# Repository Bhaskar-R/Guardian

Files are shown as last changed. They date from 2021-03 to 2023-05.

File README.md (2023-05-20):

<p align="center">
  <a href="https://github.com/Bhaskar-R/Automated-Hydroponics-System">
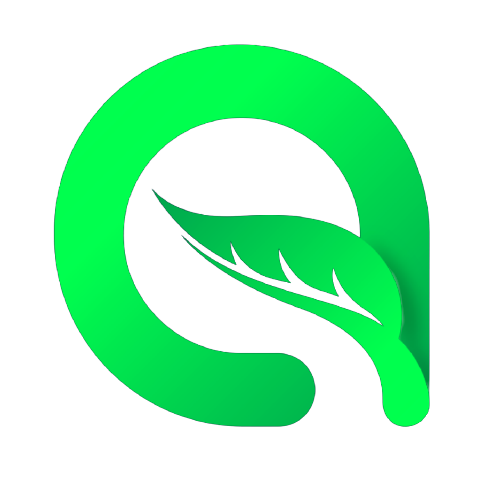
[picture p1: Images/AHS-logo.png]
AHS logo
    
  </a>
</p>

<h2 align="center">Guardian</h2>

<p align="center">Guardian is an advanced, fully automated hydroponics system designed to optimize plant growth and maximize yield. Utilizing micro-controllers and pH fuzzy logic control, it ensures precise nutrient delivery, enables remote monitoring, and achieves remarkable water savings while increasing crop productivity. 
</p>
<br>



## Table of contents
- [Render](#Render-of-Guardian)
- [Parameters Measured](#Parameters-Measured)
- [DataBase](#DataBase)
- [Controllable Parameters](#Controllable-Parameters)
    - [Motors and Light](#Motors-and-Light)
    - [Humidity and Temperature](#Humidity-and-Temperature)
    - [Light Interval](#Light-Interval)
    - [Motor Running Duration](#Motor-Running-Duration)
- [The Schematic diagram](#The-Schematic-diagram)
    - [Master Board](#The-Schematic-Diagram-of-Master-board)
    - [Slave Board](#The-Schematic-of-Slave-Board)
- [PCB Layout](#PCB-Layout)
    - [Master Board](#The-PCB-Layout-of-Master-board)
    - [Slave Board](#The-PCB-Layout-of-Slave-board)
- [Building the Hardware](#Building-the-Hardware)
    - [Master Board](#Master-Board)
    - [Total Setup](#Total-Setup-Overview)
- [I2CSB Library](#Using-`I2CSB`-library)
    - [Adding Library](#How-to-add-the-library)
    - [Functions](#How-to-use-the-functions-in-the-library)
    - [Handling the Errors and Miscommunication](#Handling-the-Errors-and-Miscommunication)
    - [Communication definitions](#The-communication-definition)
- [EEPROM Database](#Using-EEPROM-Database)
    - [Functions](#Functions)
    - [Usage](#Usage)
- [Control System](#Control-System)
- [Sample of Guardian](#Sample-of-Guardian)
- [License](#License)

## Render of Guardian
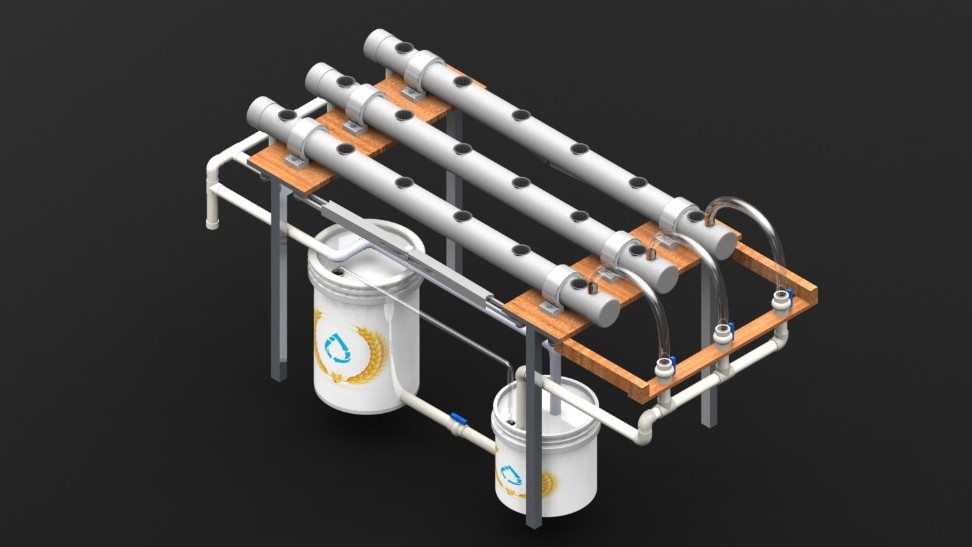
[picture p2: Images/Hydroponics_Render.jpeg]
Render


## Parameters Measured
* Temperature (DHT)
* Humidity (DHT)
* Tank Water Level
* Reservoir Water Level
* Plant Motor
* Reservoir Motor
* Mist Motor
* Lighting  

## DataBase
- Any DataBase can used to store the Data and control the System Remotely
- For this project I have used FireBase - A Realtime DataBase

A Few Pictures of FireBase
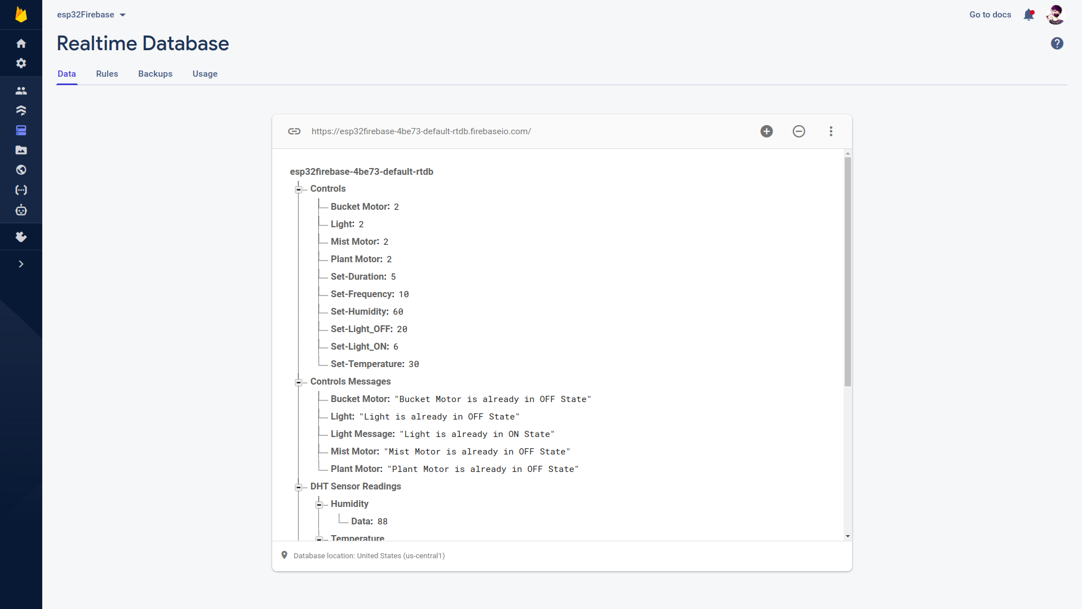
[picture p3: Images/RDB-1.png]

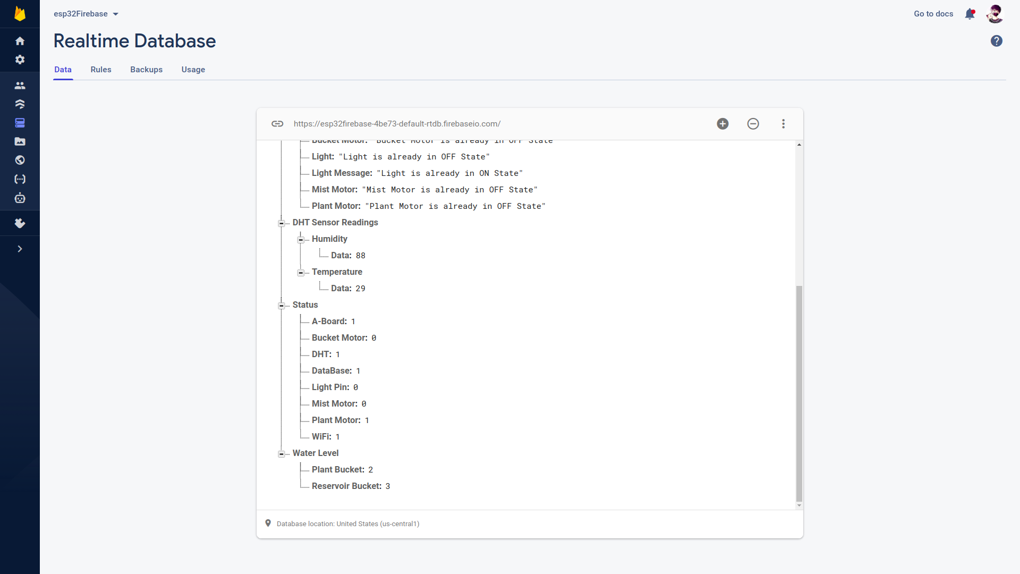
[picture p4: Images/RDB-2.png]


## Controllable Parameters  

### Motors and Light

There are two Modes for Controlling the Motors and lighting

|Digits |Status |Mode|
|---|---|----|
|0 |Off |Manual Override Mode ON | 
|1 |On |Manual Override Mode ON | 
|2 | - |Manual Override Mode OFF| 

### Humidity and Temperature

We can Manually Control/ Automate the Threshold Values of Humidity and Temperature as per the crop  

### Light Interval 
We can Manually control/ Automate the Intervals of Lighting to control the Temperature as per the requirements of the crop 

### Motor Running Duration
We can Manually control/ Automate the Intervals of running Plant Motor for regular watering as per the requirements of the crop 

## The Schematic diagram
The Schematic and PCB designs are made using KiCAD. Find the files here: [KiCad_PCB_design](PCB_designs/KiCad_PCB_design/)
### The Schematic Diagram of Master board
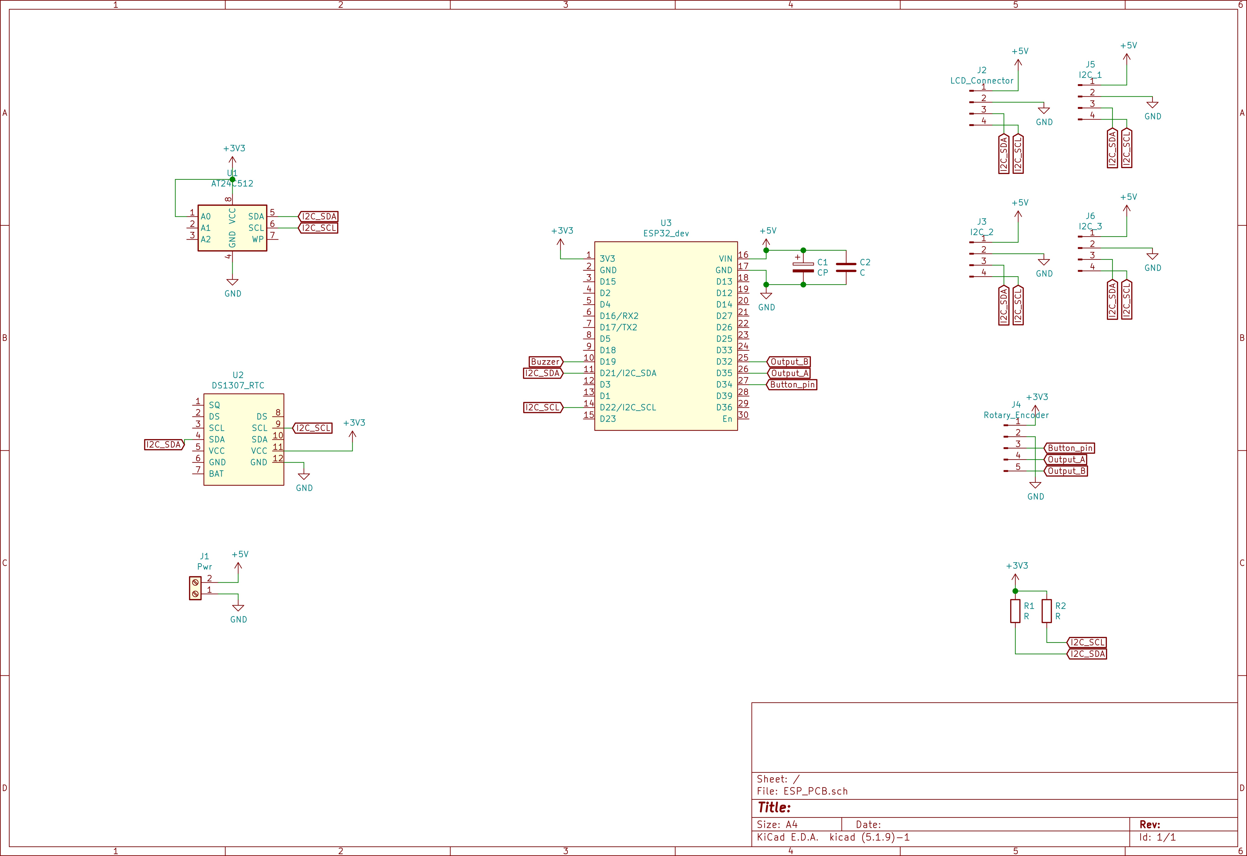
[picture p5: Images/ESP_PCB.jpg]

* The Master board has an ESP32, DS1307 RTC clock, AT24C512 EEPROM and an I2C LCD display.
* The Master board has a JST connecter port to connect to slave board. 

<br>

### The Schematic of Slave Board
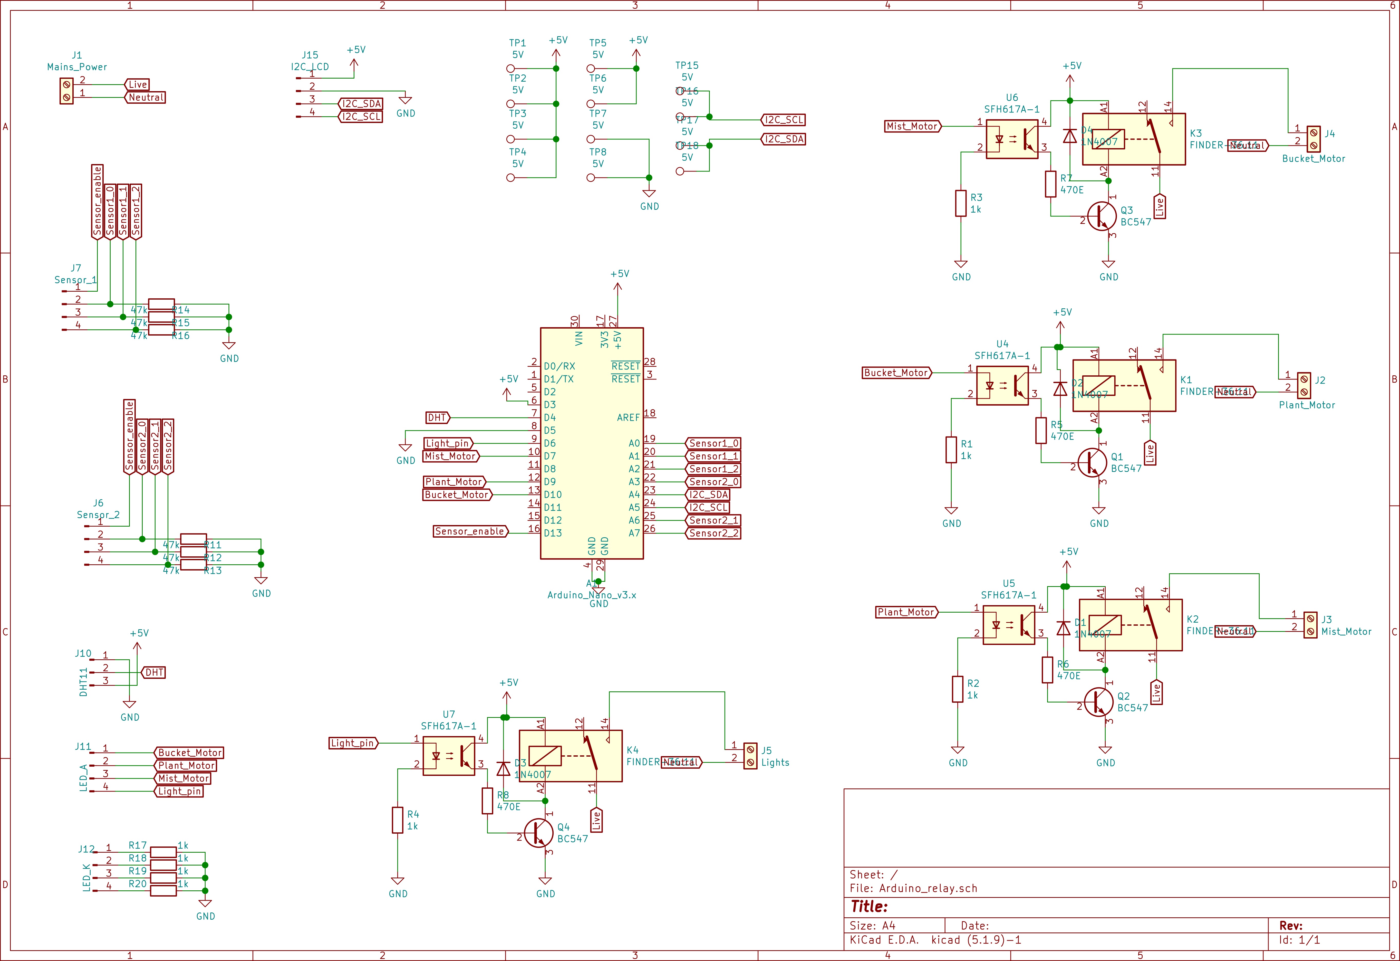
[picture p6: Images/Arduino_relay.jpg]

* The slave board has an Arduino Nano, DHT11 sensor, 4 relays. 
* The master board and slave board are connected with I2C bus.

## PCB Layout
### The PCB Layout of Master board
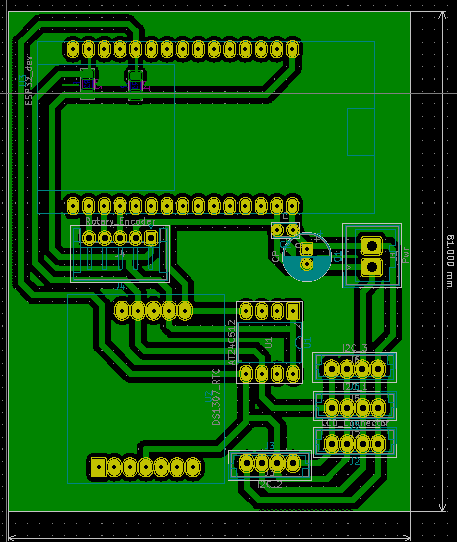
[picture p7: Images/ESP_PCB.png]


### The PCB Layout of Slave board
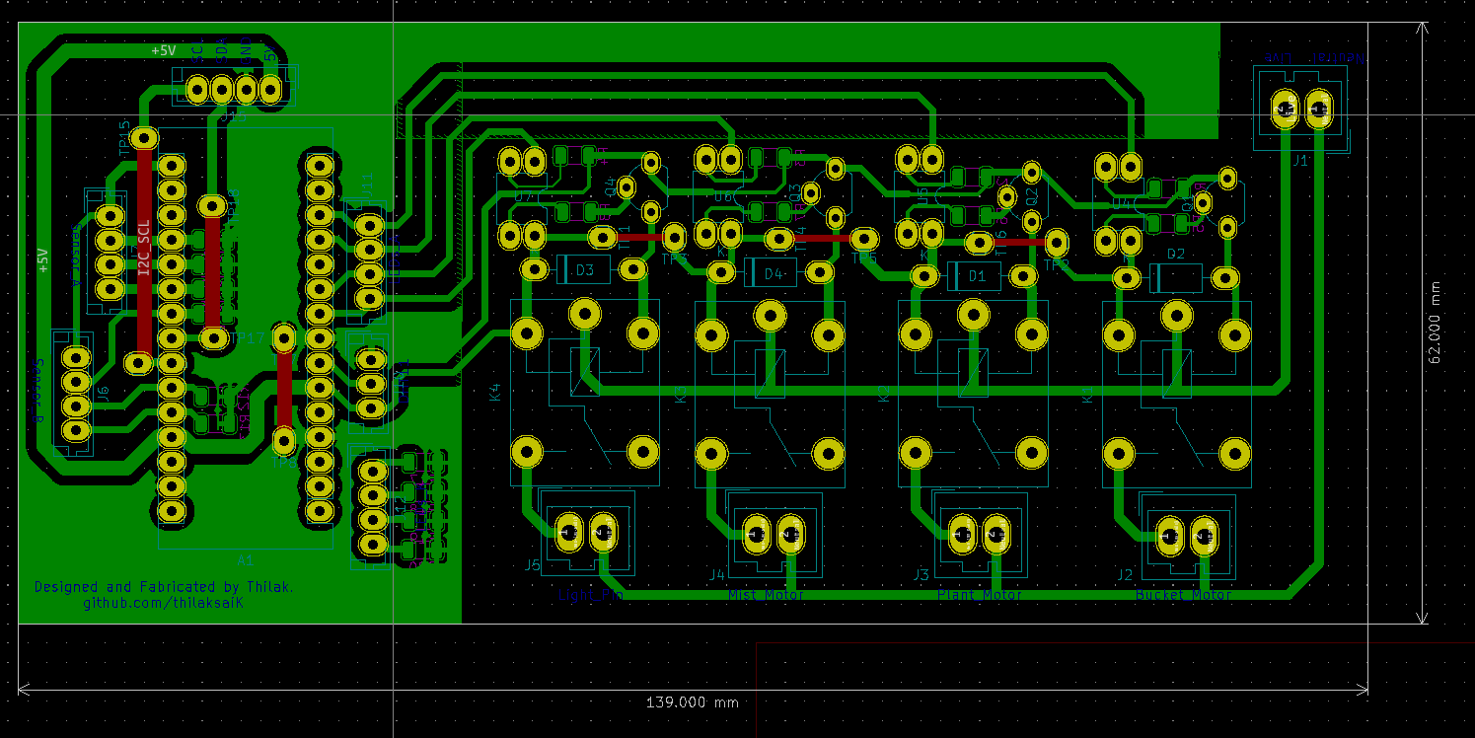
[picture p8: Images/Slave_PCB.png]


## Building the Hardware
### Master board
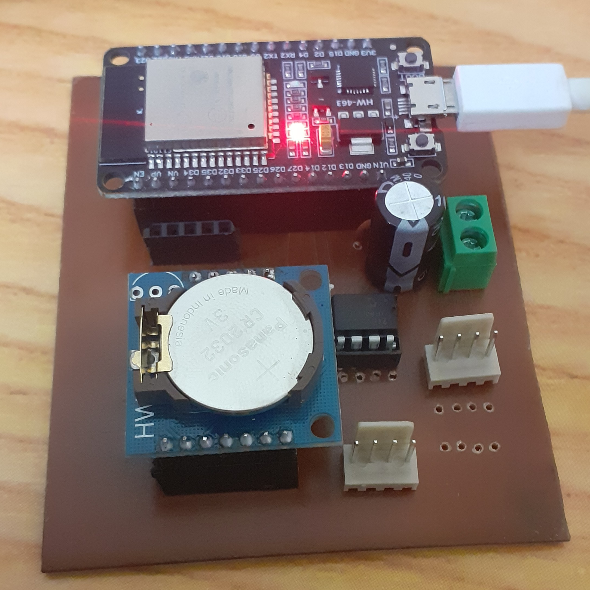
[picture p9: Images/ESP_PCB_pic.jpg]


### Total Setup Overview
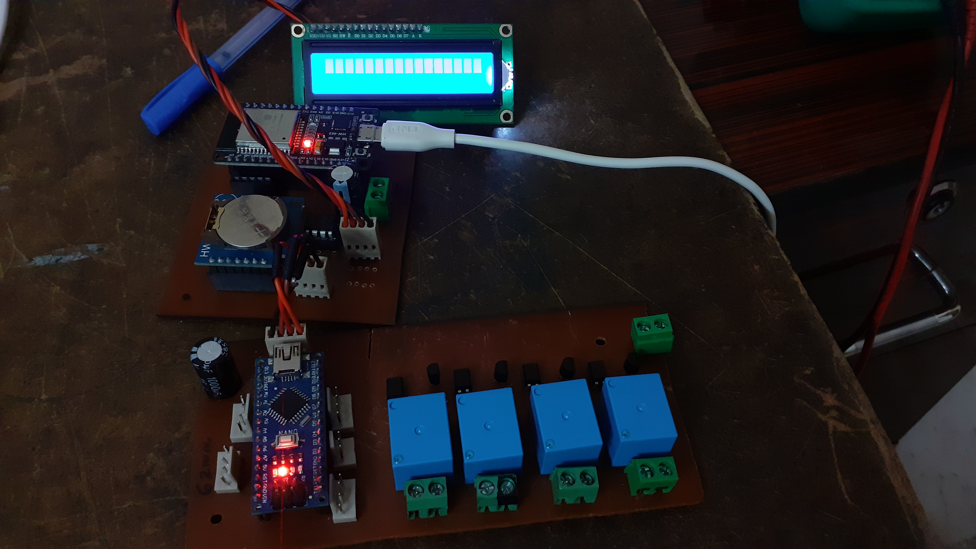
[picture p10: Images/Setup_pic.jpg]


>Find more pictures in [Images](Images) folder
## Using `I2CSB` library

This Arduino compatible library is made to simplify the communication paradigm that happens between master **ESP32** and slave **Arduino Nano**.

> I2CSB stands for I2C Slave board

The slave arduino nano does the following:
- controls 4 relays named as

1. Bucket Motor connected to pin 10
2. Plant Motor  connected to pin 9
3. Mist Motor   connected to pin 7
4. Light Pin    connected to pin 6

- Is connected to a DHT11 Temperature and Humidity sensor on pin 4.
- Has two set of water level sensors and each water level sensor can detect 3 distinct points in the used buckets.

 You can fetch the slave code here [Arduino_slave.ino](Arduino_sketches/Library/Arduino_I2C_slave/Arduino_I2C_slave.ino)
 
The Master ESP32 can access these function using the `I2CSB` Library. As the name suggests the communication happens in I2C protocol. 

### How to add the library

To use the library just navigate to [I2CSB](Arduino_sketches/Library/I2CSB/) and download it as zip file. Later in arduino IDE add this library using library manager and get started with the library using examples.

### How to use the functions in the library

1. First instantiate the class I2CSB with a slave address
```cpp
#define Slave_address 0x2F
I2CSB DB1(Slave_address);
```
2. Initialize the I2C communication by calling `Wire.begin()`

3. The library has following functions

| Function name | What is returned | return type | Arguments |
|---|---|---|---|
| 1. isConnected() |true if slave is connected | bool| no arguments|
| 2. getLevel() |Level encoded in single byte| byte| no arguments|
| 3. getTemperature() |Temperature | int  | no arguments|
| 4. getHumidity() |Humidity | int  | no arguments|
| 5. setOutputs() |`True` if the outputs are set correctly `False` if fails to set| bool | 4 bool variables|

### Handling the Errors and Miscommunication

The library also can monitor communication error or Miscommunication took place. This is how:

1. For `isConnected()` function the master sends a request to get water level. If there is no error in the received information then the function returns `True`. In the event of death of slave or the slave is not connected or there is a communication error the function returns `False`.
2. For `getLevel()` function the return type is byte and the encoded level information in the byte is as follows `x LA2 LA1 LA0 0 LB2 LB2 LB0` Here LA2,1,0 are points in sensor A and LB2,1,0 are points in Level B sensor. The `x` bit carries the error information. If there is no error in the communication then `x = 1 ` else `x = 0`.
3. For `getTemperature()` function then return type is integer. And the DHT11 sensor can measure the temperatures between 0 to 60degC with a resolution of 1degC. So the information we get out of the sensor can never hit negative temperature. So the function returns -10 if there is any error and returns value between 0 and 60 if there is no error.
4. Similarly for `getHumidity()` function, the return type is int and has values between 20 to 80. so if there is any error then the returned value will be -10.
5. For setOutputs() the return value is `True` if there is no error in communication as well as the outputs are set as expected. 
 The arguments in `setOutputs()` function is in this order `setOutputs(BucketMotor, PlantMotor, MistMotor, LightPin)`
 
 ### The communication definition
 
 * The communication is built on I2C protocol.
 * The master sends a byte contains the function the slave has to performs along with the arguments encoded in the single byte.
 * The master requests the slave 200 milliseconds later to send the fetched data/ performed action feedback encoded in 3 bytes as follows.

| Function name | Sent Byte | Received  bytes |
|---|---|---|
| 2. getLevel() | 0xAA | 0xAA 0xYY 0xYY  |
| 3. getTemperature() | 0xCA | 0xCA 0xYY 0xYY  |
| 4. getHumidity() | 0x5c | 0x5C 0xYY 0xYY  |
| 5. setOutputs() | 0x60 | 0x60 0xYY 0xYY  |
| 1. isConnected() | 0xAA | 0xAA 0xYY 0xYY  |

* The first byte is the data that is sent by master to slave so that the master can verify that slave performed correct action. and there was no miscommunication happened. 
* The second two bytes are identical. If they match then the master decides that the information received is correct and and proceeds to decode the bytes.
* The `isConnected()` function is same as `getLevel()` function with a different data type. Because I was ~lazy~ to write a new function for that purpose. 
* The example code can be found here [Example_code.ino](Arduino_sketches/Library/I2CSB/Examples/Example_code/Example_code.ino).

This library can be used as a base to make any type of simple arduino I2C slave device.

## Using EEPROM Database

Find the database library here [DataBase](Arduino_sketches/Library/DataBase/).

The data structure:
* The following data is stored in EEPROM Every minute.

| Data | Bytes taken | Range |
|---|---|---|
|Day, Hour, Minute in the month| 2 bytes | 44640|
|Temperature | 1 byte | 0 to 60 degC|
|Humidity | 1 byte | 20 to 80% |
|Level Array| 1 byte| 0x00 to 0x77|

* In a nutshell each data set consumes 5 bytes so the EEPROM can log the data for complete 9 days.
* The pointer of next address to be written locally on EEPROM because if arduino restarts the local pointer on arduino will be lost and the new data is re-written on EEPROM.
* The EEPROM used here is *AT24C512* which can store 512 Kbits or 64 KBytes which are byte addressable. So the address value range is from 0x0000 to 0xFFFF which is exactly same size that an integer(2 bytes) takes in an Arduino.
* Therefore the first two bytes in the EEPROM is reserved to write the address pointer.
* The following table represents the data structure employed.

| Address | Data |
|---|---|
| 0 , 1 | Address pointer|
| 2 - 6 | Data set 1|
| 7 - 11| Data set 2|
| 12 - 16 | Data set 3|
|(5n-3) - (5n+1) | Data set n|

### Functions

The library offers following functions:

|Function name | arguments | return value|
|---|---|---|
|[storeAt](https://github.com/thilaksaiK/Automatic_Hydroponics_V2/blob/main/README.md#storeat)|EEPROM Object, Address, Day, Hour, Minute, Temperature, Humidity, Waterlevel array| void type|
|[resetAddress](https://github.com/thilaksaiK/Automatic_Hydroponics_V2/blob/main/README.md#resetAddress)|EEPROM Object|void|
|[getDataAt](https://github.com/thilaksaiK/Automatic_Hydroponics_V2/blob/main/README.md#getDataAt)| EEPROM Object, Address, Data-literal| Data|
|[getNextAddress](https://github.com/thilaksaiK/Automatic_Hydroponics_V2/blob/main/README.md#getNextAddress)| EEPROM Object| Address of next Dataset to be written|
|[resetAddress](https://github.com/thilaksaiK/Automatic_Hydroponics_V2/blob/main/README.md#resetAddress)| EEPROM Object| resets the address pointer to initial value|
### Usage
* Include the library DataBase and [I2C_EEPROM](https://github.com/RobTillaart/Arduino/tree/master/libraries/I2C_EEPROM) on arduino IDE.
* create an I2C_eeprom object
```c++
I2C_eeprom ee(0x50, I2C_DEVICESIZE_24LC512);
```
* Create a DataBase object
```c++
DataBase DB;
```
* Begin the EEPROM object ``` ee ``` using ``` ee.begin()```.

<br>

## Control System
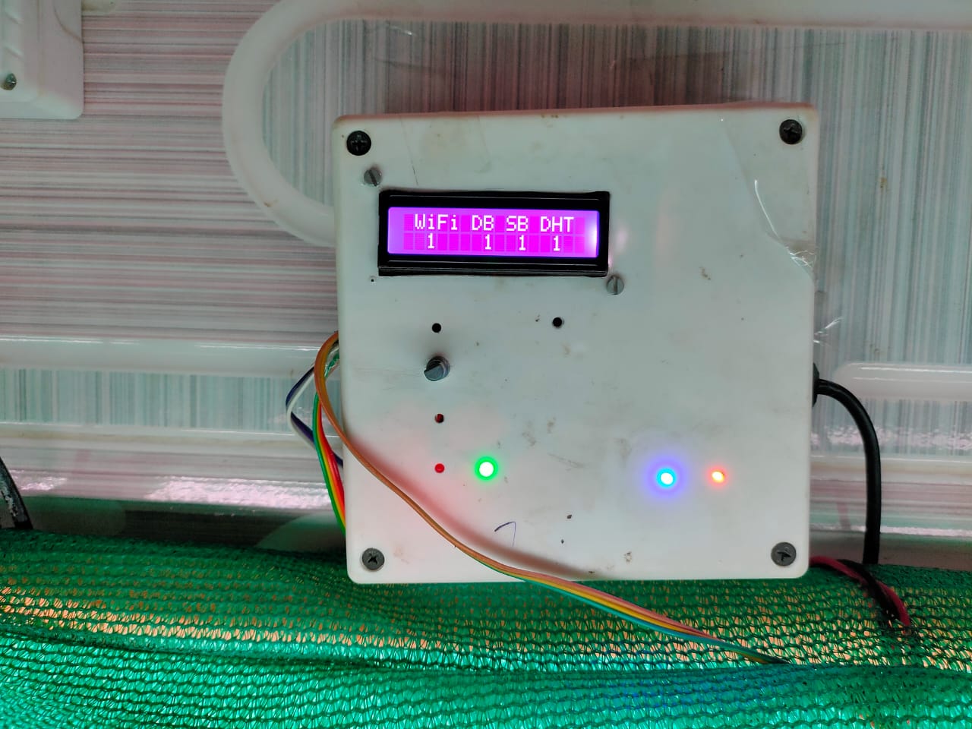
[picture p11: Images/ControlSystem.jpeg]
ControlSystem


## Sample of Guardian 
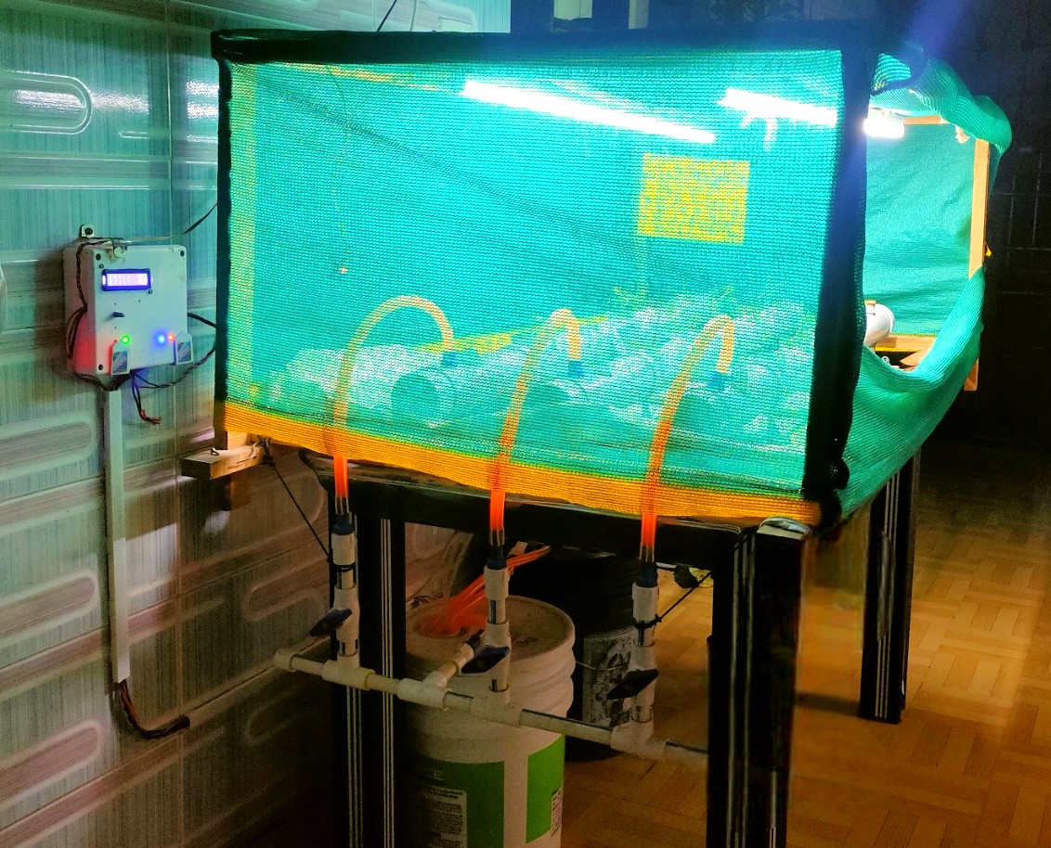
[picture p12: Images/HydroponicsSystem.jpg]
Guardian


## License
Code released under the [MIT License](https://github.com/Bhaskar-R/Automated-Hydroponics-System/blob/main/LICENSE). Docs released under [Creative Commons](https://creativecommons.org/licenses/by/3.0/).

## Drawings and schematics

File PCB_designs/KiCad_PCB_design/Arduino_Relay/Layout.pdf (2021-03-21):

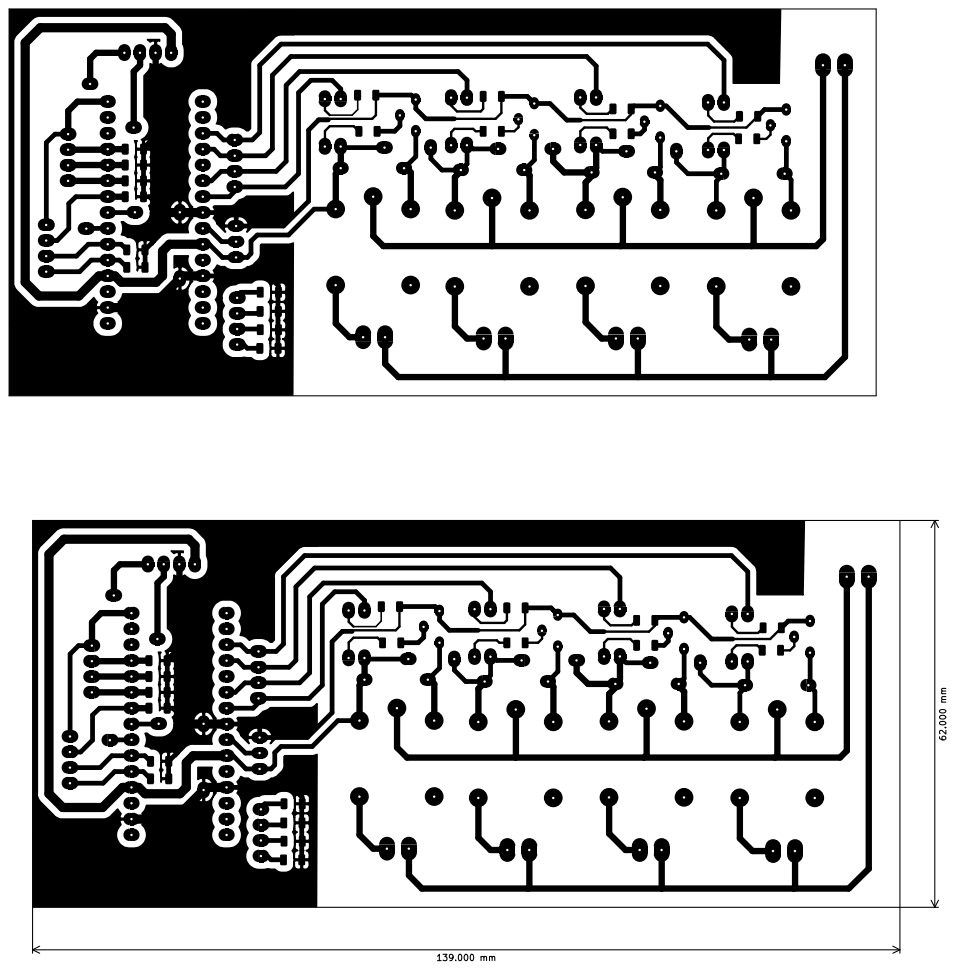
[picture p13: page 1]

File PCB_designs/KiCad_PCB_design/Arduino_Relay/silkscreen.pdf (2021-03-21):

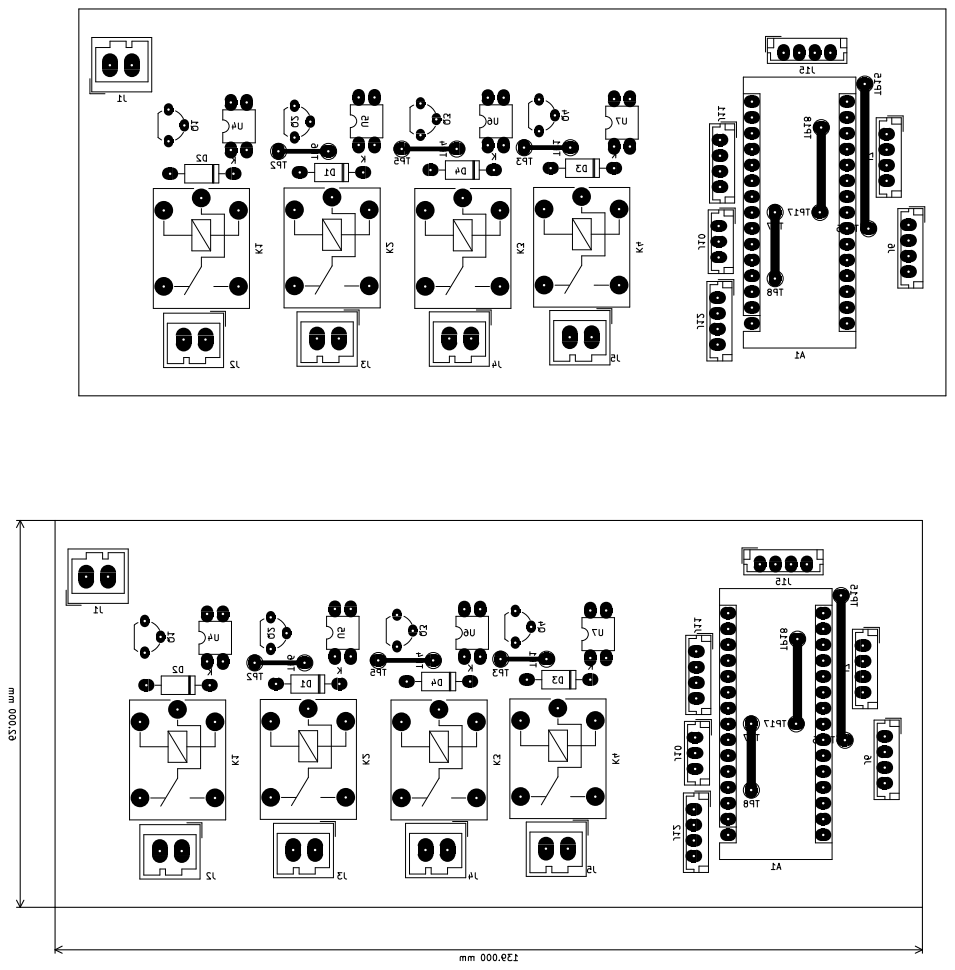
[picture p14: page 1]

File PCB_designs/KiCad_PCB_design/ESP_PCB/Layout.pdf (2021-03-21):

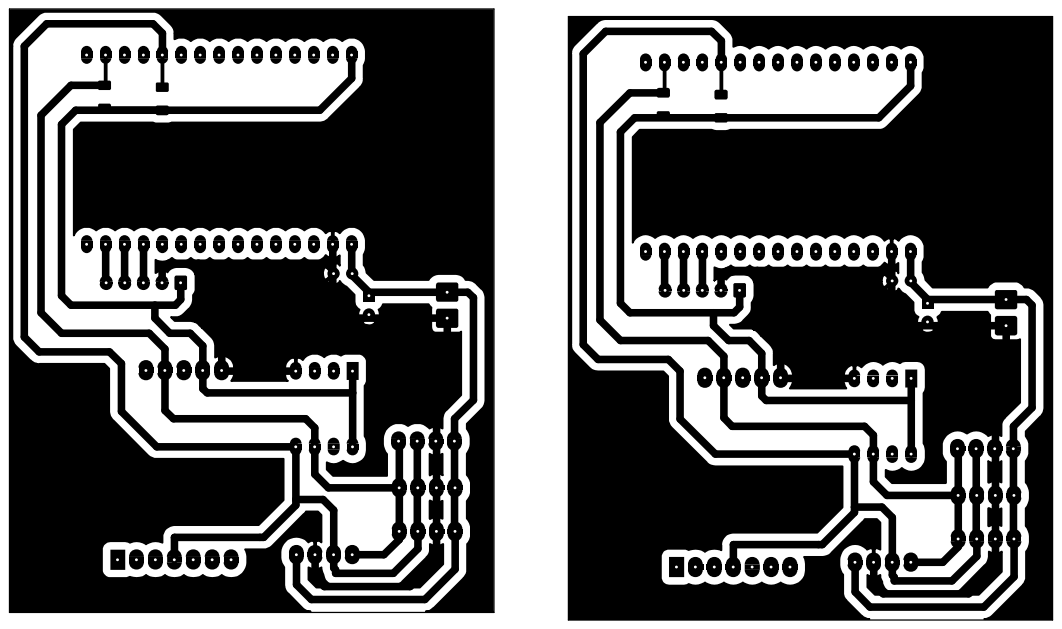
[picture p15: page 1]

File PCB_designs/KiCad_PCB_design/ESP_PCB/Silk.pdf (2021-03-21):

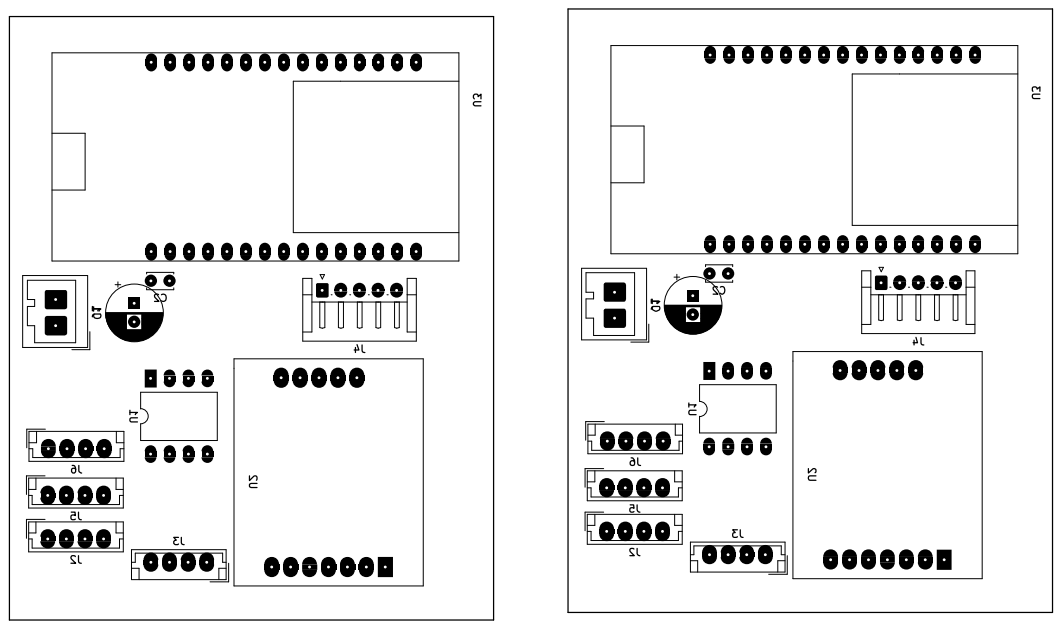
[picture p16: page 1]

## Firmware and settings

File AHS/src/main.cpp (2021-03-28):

/*
Author   - Bhaskar R
Date     - 11/03/2021
Email    - bhaskar9980@gmail.com
Github   - https://github.com/Bhaskar-R
LinkedIN - https://www.linkedin.com/in/bhaskar9980/
*/

#include <Arduino.h>
#include <LiquidCrystal_I2C.h> // LCD Display
#include <Wire.h>              // I2C Communication
#include <RTClib.h>            // Real Time Clock
#include <DataBase.h>          // EEPROM DataBase
#include <I2CSB.h>             // Slave Board - Arduino Nano
#include <I2C_eeprom.h>        // EEPROM
#include <WiFi.h>              // WIFI Module
#include <FirebaseESP32.h>     // Firebase

//Uncomment the below line for Serial debugging
//#define Serial_Debug

#define WIFI_SSID "WIFI_username"
#define WIFI_PASSWORD "WIFI_Password"

#define FIREBASE_HOST "Enter your Database URL"        // Database URL
#define FIREBASE_AUTH "Enter your Database Secret Key" //Secret Key

#define Slave_address 0x2F

//Defining the RTC clock
RTC_DS1307 RTC;

//Defining the I2C LiquidCrystal Display
LiquidCrystal_I2C lcd(0x3F, 16, 2);

//Instantiate the I2CSB Class
I2CSB SB1(Slave_address);

//Instantiate the EEPROM DataBase
DataBase DB;

//Defining the EEPROM
I2C_eeprom ee(0x51, I2C_DEVICESIZE_24LC512);

//FirebaseESP32 data object for data sending and receiving
FirebaseData fbdo;

//Global Variables
byte Seconds, Minutes, Hour, Date, Month;
bool DataCorrect;
bool PlantMotor;
bool BucketMotor;
bool MistMotor;
bool LightPin;
int ReservoirLevel;
int PlantBucketLevel;
int Humidity;
int Temperature;
int WifiStatus;
int DataBaseStatus;
int SlaveBoardStatus;
int DHTStatus;
byte Level;
byte DisplayState;
//uint8_t Fill[8] = {0xFF, 0xFF, 0xFF, 0xFF, 0xFF, 0xFF, 0xFF, 0xFF};
unsigned int InterruptTime;
int ReceivedDataProperly;

//Control Variables
int SetPlantMotor;
int SetMistMotor;
int SetBucketMotor;
int SetLight;
int SetWifi;
int DumpEEPROM;
int SetTemperature = 30;
int SetHumidity = 60;
int SetDuration = 5; //Time interval for running plant motor
int SetFrequency = 10;
int SetLightON = 6;
int SetLightOFF = 20;

String messageStatic = "Team REAPonROOF";

//Startup Display
void startupLCD()
{
    lcd.init();
    lcd.backlight();
    lcd.home();
    lcd.clear();
#ifdef Serial_Debug
    Serial.print("Automatic Plant Watering ...");
#endif
    lcd.print("SMART HYDROPONIC");
    lcd.setCursor(5, 1);
    lcd.print("SYSTEM");
    delay(700); //1000
}

//Displays the Status on the LCD Screen
void DisplayScreen()
{
    switch (DisplayState)
    {
    case 0:
        lcd.clear();
        lcd.setCursor(0, 0);
        lcd.print(" Plant   BL - ");
        lcd.print(PlantBucketLevel);
        lcd.setCursor(0, 1);
        lcd.print(" Reserve BL - ");
        lcd.print(ReservoirLevel);
        DisplayState++;
        break;
    case 1:
        lcd.clear();
        lcd.setCursor(0, 0);
        lcd.print("B P M L H - ");
        lcd.print(Humidity);
        lcd.print("%");
        lcd.setCursor(0, 1);
        lcd.print(BucketMotor);
        lcd.print(" ");
        lcd.print(PlantMotor);
        lcd.print(" ");
        lcd.print(MistMotor);
        lcd.print(" ");
        lcd.print(LightPin);
        lcd.print(" ");
        lcd.print("T - ");
        lcd.print(Temperature);
        lcd.print("C");
        DisplayState++;
        break;
    case 2:
        lcd.clear();
        lcd.setCursor(0, 0);
        lcd.print(" WiFi DB SB DHT ");
        lcd.setCursor(0, 1);
        lcd.print("  ");
        lcd.print(WifiStatus);
        lcd.print("    ");
        lcd.print(DataBaseStatus);
        lcd.print("  ");
        lcd.print(SlaveBoardStatus);
        lcd.print("  ");
        lcd.print(DHTStatus);
        lcd.print("   ");
        DisplayState++;
        break;
    case 3:
        lcd.clear();
        lcd.setCursor(0, 0);
        lcd.print("  Time   Dt Mon ");
        lcd.setCursor(0, 1);
        lcd.print(" ");
        lcd.print(Hour % 12);
        lcd.print(":");
        lcd.print(Minutes);
        lcd.print(":");
        lcd.print(Seconds);
        lcd.setCursor(9, 1);
        lcd.print(Date);
        lcd.print("  ");
        lcd.print(Month);
        lcd.print("   ");
        DisplayState++;
        break;
    case 4:
        lcd.clear();
        lcd.setCursor(7, 0);
        lcd.print("By");
        lcd.setCursor(0, 1);
        lcd.print(messageStatic);
        DisplayState = 0;
        break;
    }
}

//Firebase -- Receive Data
void ReceiveData()
{
    if (Firebase.getInt(fbdo, "/Controls/Bucket Motor", SetBucketMotor) &&
        Firebase.getInt(fbdo, "/Controls/Light", SetLight) &&
        Firebase.getInt(fbdo, "/Controls/Mist Motor", SetMistMotor) &&
        Firebase.getInt(fbdo, "/Controls/Plant Motor", SetPlantMotor) &&
        Firebase.getInt(fbdo, "/Controls/Set-Duration", SetDuration) &&
        Firebase.getInt(fbdo, "/Controls/Set-Frequency", SetFrequency) &&
        Firebase.getInt(fbdo, "/Controls/Set-Humidity", SetHumidity) &&
        Firebase.getInt(fbdo, "/Controls/Set-Light_ON", SetLightON) &&
        Firebase.getInt(fbdo, "/Controls/Set-Light_OFF", SetLightOFF) &&
        Firebase.getInt(fbdo, "/Controls/Set-Temperature", SetTemperature))
    {
        ReceivedDataProperly = 1;
    }
    else
    {
        ReceivedDataProperly = 0;
    }
#ifdef Serial_Debug
    Serial.println("Value read from database:");
    Serial.println(SetBucketMotor);
    Serial.println(SetLight);
    Serial.println(SetMistMotor);
    Serial.println(SetPlantMotor);
#endif
#ifdef Serial_Debug
    Serial.println("Data from database");
    Serial.println(Firebase.readStream(fbdo));
#endif
}
//Firebase -- Send Data
void SendData()
{
    int humidity = SB1.getHumidity();
    int temperature = SB1.getTemperature();

#ifdef Serial_Debug
    Serial.println("Database Humidity:");
    Serial.println(humidity);
#endif
    if (Firebase.setInt(fbdo, "/DHT Sensor Readings/Temperature/Data", temperature) &&
        Firebase.setInt(fbdo, "/DHT Sensor Readings/Humidity/Data", humidity) &&
        Firebase.setInt(fbdo, "/Status/Plant Motor", PlantMotor) &&
        Firebase.setInt(fbdo, "/Status/Bucket Motor", BucketMotor) &&
        Firebase.setInt(fbdo, "/Status/Mist Motor", MistMotor) &&
        Firebase.setInt(fbdo, "/Status/Light Pin", LightPin) &&
        Firebase.setInt(fbdo, "/Status/WiFi", WifiStatus) &&
        Firebase.setInt(fbdo, "/Status/DataBase", DataBaseStatus) &&
        Firebase.setInt(fbdo, "/Status/A-Board", SlaveBoardStatus) &&
        Firebase.setInt(fbdo, "/Status/DHT", DHTStatus) &&
        Firebase.setInt(fbdo, "/Water Level/Plant Bucket", PlantBucketLevel) &&
        Firebase.setInt(fbdo, "/Water Level/Reservoir Bucket", ReservoirLevel))
    {
        DataBaseStatus = 1;
    }
    else
    {
        DataBaseStatus = 0;
#ifdef Serial_Debug
        Serial.println("Error in Sending Data to Database - ");
        Serial.println(fbdo.errorReason());
#endif
    }

    if (isnan(humidity) || isnan(temperature))
    {
        DHTStatus = 0;
#ifdef Serial_Debug
        Serial.println("Failed to read from DHT sensor!");
#endif
        return;
    }
    else
        DHTStatus = 1;
}

//Store Data in eeprom if the wifi is off
void StoreDate()
{
    if (DataBaseStatus == 0 || WifiStatus == 0)
    {
        DB.storeAt(ee, 2, Date, Hour, Minutes, Temperature, Humidity, Level);
    }
}

// Updates the time on the screen
void timeUpdate()
{
#ifdef Serial_Debug
    Serial.println("Updating time");
#endif
    DateTime now = RTC.now();
    Seconds = now.second();
    Minutes = now.minute();
    Hour = now.hour();
    Date = now.day();
    Month = now.month();
#ifdef Serial_Debug
  Serial.print(now.twelveHour();
  Serial.print(":");
  Serial.print(now.minute());
  Serial.print(":");
  Serial.print(now.second());
  Serial.println("\t \t Done!");
#endif
}

void setup()
{

    WiFi.begin(WIFI_SSID, WIFI_PASSWORD);
    while (WiFi.status() != WL_CONNECTED)
    {
        delay(500); //500
    }
    if (WiFi.status() == WL_CONNECTED)
        WifiStatus = 1;
    else
        WifiStatus = 0;
    Wire.begin();
    RTC.begin();
    startupLCD();
    //RTC.adjust(DateTime(__DATE__, __TIME__));
    delay(1500); //2000
    lcd.clear();
    ee.begin();
    Serial.begin(115200);
    Serial.println(WiFi.localIP());

    //--------- Firebase Auth -----------
    Firebase.begin(FIREBASE_HOST, FIREBASE_AUTH);
    Firebase.reconnectWiFi(true);

    InterruptTime = millis();
    DisplayScreen();
}
void loop()
{
    timeUpdate();

    // For LCD Display
    while (millis() - InterruptTime > 500)
    {
        DisplayScreen();
        InterruptTime = millis();
    }

    DataCorrect = 1;
    if (SB1.isConnected() == 1)
    {
        SlaveBoardStatus = 1;
        unsigned long TimeoutTrack = millis();
        do
        {
#ifdef Serial_Debug
            Serial.print("Get Level\t");
#endif
            Level = SB1.getLevel(); // x LA2 LA1 LA0 0 LB2 LB1 LB0  -- A => Plant Bucket B => Reservoir Bucket
#ifdef Serial_Debug
            Serial.println(Level, BIN);
#endif

        } while ((!(Level & 0x80)) && (millis() - TimeoutTrack < 10000));
        DataCorrect &= (millis() - TimeoutTrack < 10000);

        //Reservoir Levels
        ReservoirLevel = 0;
        if ((Level & 7) == 7)
            ReservoirLevel = 3;

        else if ((Level & 7) == 3)
            ReservoirLevel = 2;

        else if ((Level & 7) == 1)
            ReservoirLevel = 1;

        //Plant Bucket Levels
        PlantBucketLevel = 0;
        if (((Level >> 4) & 7) == 7)
            PlantBucketLevel = 3;

        else if (((Level >> 4) & 7) == 3)
            PlantBucketLevel = 2;

        else if (((Level >> 4) & 7) == 1)
            PlantBucketLevel = 1;

#ifdef Serial_Debug
        Serial.print("Plant Bucket Level \t");
        Serial.println(PlantBucketLevel);
        Serial.print("Reservoir Level \t");
        Serial.println(ReservoirLevel);
#endif
        //Bucket Motor
        if (PlantBucketLevel == 1 && BucketMotor == 0 && ReservoirLevel > 1)
        {
            BucketMotor = 1;
        }
        if ((PlantBucketLevel == 3 && BucketMotor == 1) || ReservoirLevel <= 1)
        {
            BucketMotor = 0;
        }

        //Manual Overriding of Bucket Motor
        if (SetBucketMotor == 1)
        {
            if (BucketMotor == 1)
            {
                Firebase.setString(fbdo, "/Controls Messages/Bucket Motor", "Bucket Motor is already in ON State");
            }
            else
            {
                if (PlantBucketLevel == 3)
                {
                    Firebase.setString(fbdo, "/Controls Messages/Bucket Motor", "Plant Bucket is already at Level-3");
                }
                else
                    BucketMotor = 1;
            }
            if (BucketMotor == 1)
                SetBucketMotor = 2;
        }
        if (SetBucketMotor == 0)
        {
            if (BucketMotor == 0)
            {
                Firebase.setString(fbdo, "/Controls Messages/Bucket Motor", "Bucket Motor is already in OFF State");
            }
            else
            {
                if (PlantBucketLevel == 3)
                {
                    Firebase.setString(fbdo, "/Controls Messages/Bucket Motor", "Plant Bucket is Filled Upto Level-3");
                    BucketMotor = 0;
                }
                else
                {
                    Firebase.setString(fbdo, "/Controls Messages/Bucket Motor", "Plant Bucket is not filled Upto Level-3");
                    BucketMotor = 0;
                }
            }
        }

        // Plant Motor
        if (((Minutes) % SetFrequency < SetDuration) && PlantMotor == 0)
        {
            PlantMotor = 1;
        }
        if (((Minutes) % SetFrequency >= SetDuration) && PlantMotor == 1)
        {
            PlantMotor = 0;
        }

        //Manual Overriding of Plant Motor
        if (SetPlantMotor == 1)
        {
            if (PlantMotor == 1)
            {
                Firebase.setString(fbdo, "/Controls Messages/Plant Motor", "Plant Motor is already in ON State");
            }
            else
                PlantMotor = 1;
            if (PlantMotor == 1)
                SetPlantMotor = 2;
        }
        if (SetPlantMotor == 0)
        {
            if (PlantMotor == 0)
            {
                Firebase.setString(fbdo, "/Controls Messages/Plant Motor", "Plant Motor is already in OFF State");
            }
            else
                PlantMotor = 0;
        }

        //Light
        if ((SetLightON <= Hour) && (Hour < SetLightOFF) && LightPin == 0)
        {
            LightPin = 1;
        }
        if ((SetLightOFF <= Hour) && LightPin == 1)
        {
            LightPin = 0;
        }

        //Manual Overriding of Lights
        if (SetLight == 1)
        {
            if (LightPin == 1)

            {
                Firebase.setString(fbdo, "/Controls Messages/Light", "Light is already in ON State");
            }
            else
                LightPin = 1;
            if (LightPin == 1)
                SetLight = 2;
        }
        if (SetLight == 0)
        {
            if (LightPin == 0)
            {
                Firebase.setString(fbdo, "/Controls Messages/Light", "Light is already in OFF State");
            }
            else
                LightPin = 0;
        }

        TimeoutTrack = millis();
        do
        {
#ifdef Serial_Debug
            Serial.print("Get Humidity\n");
#endif

            Humidity = SB1.getHumidity();
            delay(700); //1000

#ifdef Serial_Debug
            Serial.print("%d\n", Humidity);
#endif
        } while ((millis() - TimeoutTrack < 10000) && (Humidity == -1));
        DataCorrect &= (millis() - TimeoutTrack < 10000);

        TimeoutTrack = millis();
        do
        {
#ifdef Serial_Debug
            Serial.print("Get Temperature\n");
#endif

            Temperature = SB1.getTemperature();
            delay(700); //1000

#ifdef Serial_Debug
            Serial.print("%d\n", temperature);
#endif
        } while ((millis() - TimeoutTrack < 10000) && (Temperature == -1));
        DataCorrect &= (millis() - TimeoutTrack < 10000);

        if ((Temperature != -1) && (Humidity != -1))
        {
            //Humidity
            if (Humidity <= SetHumidity && MistMotor == 0)
            {
                MistMotor = 1;
            }

            //Temperature
            if (Temperature >= SetTemperature && MistMotor == 0)
            {
                MistMotor = 1;
            }
            if (Temperature < SetTemperature && MistMotor == 1 && Humidity > SetHumidity)
            {
                MistMotor = 0;
            }
        }
        else
        {
            DataCorrect = 0;
        }

        TimeoutTrack = millis();
        do
        {
#ifdef Serial_Debug
            Serial.print("Set outputs\n");
#endif
            delay(700); //1000
        } while ((millis() - TimeoutTrack < 10000) && !SB1.setOutputs(LightPin, MistMotor, PlantMotor, BucketMotor));
        DataCorrect &= (millis() - TimeoutTrack < 10000);

        Serial.printf("B = %d, P = %d, M = %d, L = %d\n", BucketMotor, PlantMotor, MistMotor, LightPin);

        //Manual Overriding of Mist Motor
        if (SetMistMotor == 1)
        {
            if (MistMotor == 1)
            {
                Firebase.setString(fbdo, "/Controls Messages/Mist Motor", "Mist Motor is already in ON State");
            }
            else
                MistMotor = 0;
            if (MistMotor == 1)
                SetMistMotor = 2;
        }
        if (SetMistMotor == 0)
        {
            if (MistMotor == 0)
            {
                Firebase.setString(fbdo, "/Controls Messages/Mist Motor", "Mist Motor is already in OFF State");
            }
            else
                MistMotor = 0;
        }

        if (DataCorrect)
        {
#ifdef Serial_Debug
            Serial.print("All Data is correct and sending to Firebase\n\n");
#endif
            SendData();
            ReceiveData();
        }
        else
        {
#ifdef Serial_Debug
            Serial.print("Data is wrong!\n\n");
#endif
        }
    }
    else
        SlaveBoardStatus = 0;
}

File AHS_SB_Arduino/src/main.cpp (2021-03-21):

#include <Arduino.h>
#include <Wire.h>
#include "DHT.h"

//Uncomment the below line to debug
//#define Debug

#define Bucket_Motor 10
#define Plant_Motor 9
#define Mist_Motor 7
#define Light_pin 6
#define DHTPIN 4
#define Data_out 13
#define Threshold 600
#define DHTTYPE DHT11

byte c;

int sendState = 0;
#define Slave_address 0x2F

bool flag;
byte sendBytes[3];
bool Levels_bool[6];
const int Level_pins[6] = {A0, A1, A2, A3, A6, A7};
int Temperature, Humidity;

int getHumidity();
int getTemp();
void receiveEvent(int);
void requestEvent();
DHT dht(DHTPIN, DHTTYPE);
void setup()
{
  Serial.begin(9600);
#ifdef Debug
  Serial.println("Debugging serial has started");
#endif
  pinMode(Bucket_Motor, OUTPUT);
  pinMode(Plant_Motor, OUTPUT);
  pinMode(Mist_Motor, OUTPUT);
  pinMode(Light_pin, OUTPUT);
  pinMode(Data_out, OUTPUT);
  dht.begin();
  for (int i = 0; i < 6; i++)
    pinMode(Level_pins[i], INPUT);

  Wire.begin(Slave_address);
  Wire.onRequest(requestEvent);
  Wire.onReceive(receiveEvent);
  Humidity = dht.readHumidity();
  Temperature = dht.readTemperature();
#ifdef Debug
  Serial.println("Temperature read");
#endif
}
unsigned long PreviousMillis;
void loop()
{
  if (millis() - PreviousMillis > 60000)
  {
    PreviousMillis = millis();
    Humidity = dht.readHumidity();
    Temperature = dht.readTemperature();
#ifdef Debug
    Serial.println("Temperature readed");
#endif
  }
  if (flag)
  {
    sendState = 0;
    long entry = millis();
    while (Wire.available() > 0 && (millis() - entry < 100))
    {
      c = Wire.read();
#ifdef Debug
      Serial.print("Received = 0x");
      Serial.println(c, HEX);
#endif
    }
    int Select = c >> 4;
#ifdef Debug
    Serial.print("Case = ");
    Serial.println(Select);
#endif

    if (Select == 5)
    {
      sendBytes[0] = c;
      sendBytes[1] = map(dht.readHumidity(), 20, 80, 100, 220);
      sendBytes[2] = sendBytes[1];
#ifdef Debug
      Serial.println("******************Get Humidity****************");
      Serial.print("Read Humidity = ");
      Serial.print(Humidity);
      Serial.print("\t Packed byte = ");
      Serial.println(sendBytes[1]);
#endif
    }

    else if (Select == 6)
    {
      digitalWrite(Bucket_Motor, (c)&0x01);
      digitalWrite(Plant_Motor, (c >> 1) & 0x01);
      digitalWrite(Mist_Motor, (c >> 2) & 0x01);
      digitalWrite(Light_pin, (c >> 3) & 0x01);
      sendBytes[0] = 0x60;
      sendBytes[0] |= digitalRead(Bucket_Motor);
      sendBytes[0] |= digitalRead(Plant_Motor) << 1;
      sendBytes[0] |= digitalRead(Mist_Motor) << 2;
      sendBytes[0] |= digitalRead(Light_pin) << 3;
#ifdef Debug
      Serial.println("*********Toggle Outputs***********");
      Serial.println("Buck\tPlant\tMist\tLight");
      Serial.print((c)&0x01);
      Serial.print("\t");
      Serial.print((c >> 1) & 0x01);
      Serial.print("\t");
      Serial.print((c >> 2) & 0x01);
      Serial.print("\t");
      Serial.println((c >> 3) & 0x01);
      Serial.print("Send byte = ");
      Serial.println(sendBytes[0], HEX);
#endif
      sendBytes[1] = sendBytes[0];
      sendBytes[2] = sendBytes[1];
    }
    else if (Select == 10)
    {
      digitalWrite(Data_out, HIGH);
      sendBytes[0] = c;
#ifdef Debug
      Serial.println("*********Read Levels***********");
#endif
      for (int i = 0; i < 6; i++)
      {
        Levels_bool[i] = analogRead(Level_pins[i]) > Threshold;
        delay(100);
#ifdef Debug
        Serial.print(Levels_bool[i]);
        Serial.print("\t");
#endif
      }
#ifdef Debug
      Serial.println();
#endif

      sendBytes[1] = 0;
      sendBytes[2] = 0;

      for (int i = 0; i < 3; i++)
        sendBytes[1] |= Levels_bool[i] << i;

      for (int i = 3; i < 6; i++)
        sendBytes[1] |= Levels_bool[i] << (i + 1);

      sendBytes[2] = sendBytes[1];
#ifdef Debug
      Serial.print("Packed byte = ");
      Serial.println(sendBytes[1], BIN);
#endif
      digitalWrite(Data_out, LOW);
    }
    if (Select == 12)
    {
      sendBytes[0] = c;
      sendBytes[1] = map(dht.readTemperature(), 0, 50, 100, 200);
#ifdef Debug
      Serial.println("******************Get Temperature*************");
      Serial.print("Read temperature = ");
      Serial.print(Temperature);
      Serial.print("\t Packed byte = ");
      Serial.println(sendBytes[1]);
#endif
      sendBytes[2] = sendBytes[1];
    }
    flag = 0;
  }
}
void receiveEvent(int)
{
  flag = 1;
}
void requestEvent()
{
  if (sendState == 3)
    sendState = 0;
  Wire.write(sendBytes[sendState]);
  sendState++;
}
